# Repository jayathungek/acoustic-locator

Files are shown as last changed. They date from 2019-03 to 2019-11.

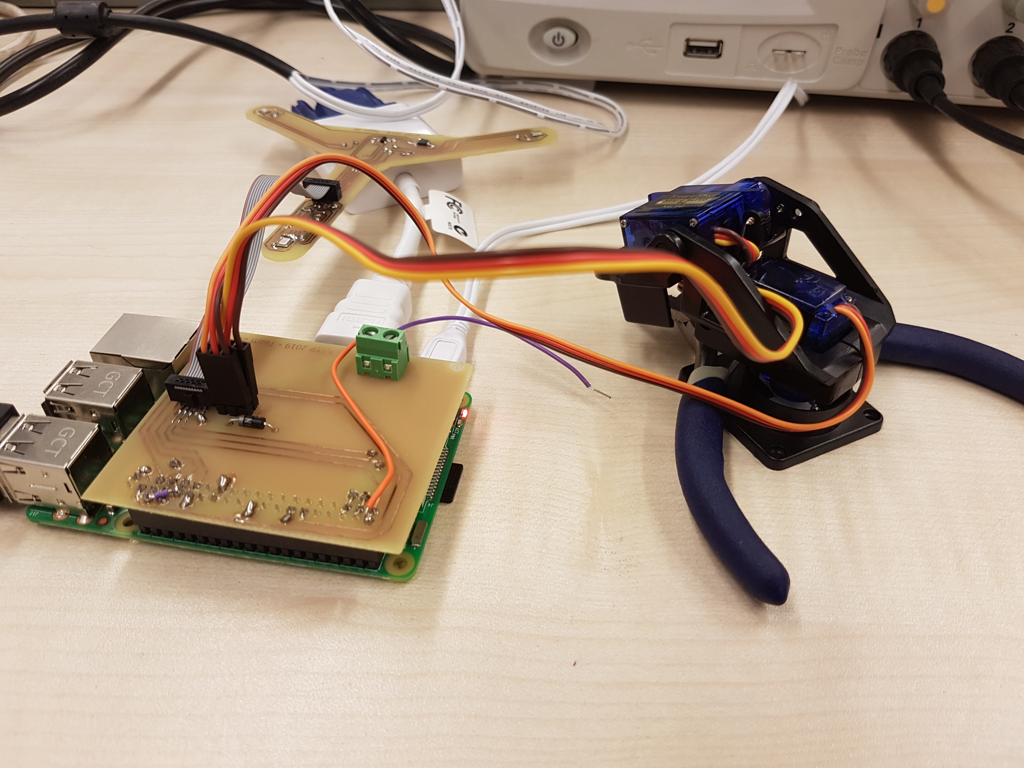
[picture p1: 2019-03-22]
Media/20190313_165925.jpg

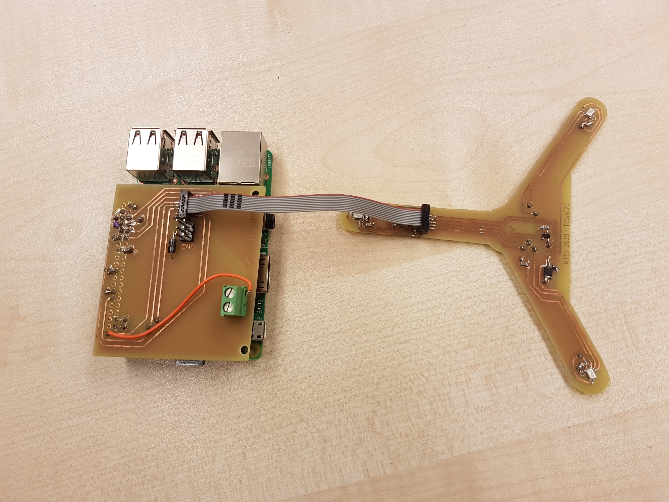
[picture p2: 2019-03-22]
Media/20190313_170128.jpg

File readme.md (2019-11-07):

Table of Contents
=================

   * [acoustic-locator](#acoustic-locator)
      * [Hardware setup](#hardware-setup)
        * [The Microphone Circuit](#the-microphone-circuit)
        * [The Humidity/Temperature Sensor](#the-humiditytemperature-sensor)
        * [The Laser LED circuit](#the-laser-led-circuit)
        * [The Servo Circuit](#the-servo-circuit)
        * [Mechanical Design](#mechanical-design)
      * [Prerequisites](#prerequisites)
      * [Installation](#installation)
      * [How to use](#how-to-use)
      
# acoustic-locator

## Hardware setup

The acoustic locator hardware consists of two basic modules. The first module is the microphone module build on a PCB board that enables the placement of three MEMS microphones. The second module is the positioning module which consists basically of two servo motors, one being responsible for the horizontal movement of the mechanism and the other for the vertical. The front and back views of the acoustic locator are shown in figure 1. The sound source direction detection is achieved with the use of three microphones forming an equilateral triangle. The three holes at the edges of the acoustic locator identified on the front view are the openings for the three microphones. The opening in the middle of the acoustic locator, shown in the front view is the opening for the laser diode. The back view shows the positioning mechanism with the two servo motors.

AL picture

                            Figure 1
                            
 The PCB board for the microphones is shown in figure 2. An IDC connector is used to connect the board with the Raspberry Pi board. The microphones used are Integrated Inter-IC Sound Bus (I2S) compatible digital MEMS microphones. I2S is a serial bus standard/protocol that enable the interface of one or two microphones on a microcontroller through a serial connection. Since the acoustic locator uses three microphones, a multiplexer is used to enable the connection of the microphones on the I2S bus. 

The microphones board also contains the circuit for the humidity/temperature sensor. The reason for using this sensor is because the speed of sound can vary with the temperature and the humidity. If the acoustic locator is used in normal room conditions then there is no need for the temperature/humidity sensor. If the acoustic locator is going to be used in places with extreme temperatures or humidity then the values of the temperature and humidity can be used to calculate the speed of sound and adjust the operation of the acoustic locator accordingly. 

The third module on the microphones PCB board is a laser LED circuit consisting of a LED driver and the laser LED. The laser LED is used for testing purposes, in order to identify the direction at which the acoustic locator is pointing to. On the final product, the laser LED can be replaced by a web camera, so that the camera will point to the person speaking, as explained in the introduction of this report.

Mic_Board

                            Figure 2
                            
### The Microphone Circuit

The microphones used by the acoustic locator are the ICS-43432 digital I2S microphones from InvenSence. The ICS-43432 microphone includes all the required circuitry so that it can be interfaced directly with a microcontroller or a DSP, without the use of an audio codec. As shown in figure 3 the ICS-43432 contains in the same package the MEMS sensor with the signal conditioning circuit, the A/D converter, the anti-aliasing filter and a 24-bit I2S interface. The data sheet, handling information and application notes for the ICS-43432 microphone can be found [here]( https://www.invensense.com/products/digital/ics-43432/).

The ‘Config’ input is used in cases where it is required to modify the internal registers of the device. For normal operation, the ‘Config’ signal must be connected to the ground.  The ‘Left/Right’ (LR) channel select signal is used to specify to which one of the two I2S channels is the microphone connected to. If the L/R pin is connected to the ground (or set to Low), the microphone outputs its signal to the left channel of the I2C frame. If the L/R pin is connected to the supply voltage (or set to High), the microphone outputs its signal to the right channel of the I2C frame.

The I2C signals are the ‘SCK’ (Serial Data Clock for the I2S interface) input signal, the ‘SD’ (Serial Data Output for the I2S interface) signal and the ‘WS’ (Serial Data Word Select for the I2S interface) input signal. If the ‘WS’ signal is set Low, the left microphone sends its data on the ‘SD’ signal, otherwise the right microphone sends its data. The ‘SD’ line must be pull down to the ground using a 100K resistor. A typical circuit with two microphones connected to a DSP or a microcontroller is shown in figure 4.

ICS43432

                              Figure 3
                              
Stereo                              
            
                              Figure 4
                              
The circuit diagram of the acoustic locator microphone board is shown in figure 5. Because the acoustic locator uses three microphones and the I2S interface supports only two, a demultiplexer is used to allow two microphone to share the same I2S channel. The demultiplexer used is the TS3A24159 dual 2-channel SPDT bidirectional analogue switch. As shown in the circuit diagram, the select input (In1) of the analogue switch is connected to the GPIO9 signal of the Raspberry Pi, while the Com input is connected to the WS signal (signal GPIO19).

Setting the In1 pin to low, the WS signal is switched to the WS signal of the Mic1 microphone, thus reading the data from Mic1.  Setting the In1 pin to high, the WS signal is switched to the WS signal of the Mic2 microphone, thus reading the data from Mic2. Since the LR inputs for Mic1 and Mic2 are connected to the supply voltage, both microphones are treated as Right channel microphones. The LS signal of microphone Mic3 is connected to the ground, therefore, this microphone is treated as the Left channel microphone.

Mic_board_Cct(1)

                              Figure 5

### The Humidity/Temperature Sensor

The Humidity/Temperature Sensor used by the acoustic locator is the HIH6030-021-001 digital I2C humidity/temperature from Honeywell. This device combines a humidity and a temperature sensor in the same package. The data sheet, handling information and application notes for the HIH6030-021-001 digital I2C humidity/temperature can be found [here](https://sensing.honeywell.com/HIH6030-021-001-humidity-sensors). 

The pinout with the typical application circuit diagram, given in the device datasheet is shown in figure 13.The same circuit is used  by the acoustic locator as shown in the circuit diagram in figure 5.The SCL pin is connected to the I2C clock, while the SDA pin is connected to the I2C data line. Both the SCL and the SDA pins must be pulled up with a 2.2K resistor each. The supply pin must be decoupled with a 0.1µF capacitor, while the Vcore pin must be connected to the ground through a 0.22µF capacitor. The AL_L (Alarm Low) and the AL_H (Alarm High) pins are used in the case an external device such as a relay or a LED are needed to be controlled directly by the sensor.

Hum_cct

                                Figure 6
                                                           
### The Laser LED circuit

The laser LED circuit, shown in figure 7, consists of the laser diode, MOSFET transistor driver and resistor. The transistor driver is used because the Raspberry Pi cannot provide the amount of current required to operate the laser LED. The resistor is used to limit the current through the laser to the value lower than the maximum LED current. The operation of the laser is achieved by controlling the state of the GPIO6 of the Raspberry Pi.

laser

                                Figure 7
                                
### The Servo Circuit

The movement of the positioning mechanism is achieved by the use of two servo motors. These motors are connected by the Raspberry Pi, through a board that is attached on the Raspberry Pi as a shield shown in figure 8. This shield also provides a connection from the Raspberry Pi to the microphones board through an IDC connector and a ribbon cable.The circuit diagram for the connection of the two servo motors to the Raspberry Pi is shown in figure 9. The speed and direction of rotation of the servo motors is achieved through the PWM signals obtained from the GPIO12 and the GPIO13 signals of the Raspberry Pi.

RPShield

                                Figure 8
                                
servocct

                                Figure 9
                                
### Mechanical Design

The mechanical design consists of the direction mechanism. This design features three parts: (a) the base, (b) a gimbal and (c) the head.

The base serves two functions: it supports the device as well as houses the Raspberry Pi, along with the locator interface board. The design allows the Raspberry Pi to be connected to a PC/laptop without opening the base.
The pan/tilt gimbal aids the movement of the device. It is capable of 180° rotation around the vertical axis as well as 100° up and down. The gimbal is mounts on top of the base as well as holding the head.

The head – a 3D printed part – clicks in place on top of the gimbal. The part is designed to secure the microphones in their respective places. The PCB just slides intro the head, thus no screws are required to hold the electronics on the gimbal.

## Prerequisites
The following steps are needed to configure the raspberry pi for I2S microphone support:

1. Enable I2S communication:- 
  ```
  $ sudo nano /boot/config.txt
  ```
  1.1 Navigate the file and uncomment the the line that contains `#dtparam=i2s=on`. 
  
2. Add the reference for the chip on the Raspberry Pi 3 that handles the I2S into the modules file:- 
  ```
  $ sudo nano  /etc/modules
  ``` 
  2.1 Add the line `snd-bcm2835` to this file.
  
3. Reboot:- 
  ```
  $ sudo reboot
  ```
  
4. Run this command and verify that it outputs `snd_soc_bcm2835_i2s`:-
  ```
  $ lsmod | grep snd
  ```
  
5. Install dependancies and set permissions:- 
  ```
  $ sudo apt-get -y install bc libncurses5-dev
  $ sudo wget https://raw.githubusercontent.com/notro/rpi-source/master/rpi-source -O /usr/bin/rpi-source`
  $ sudo chmod +x /usr/bin/rpi-source
  ```
6. Update `rpi-source` and run:-
  ```
  $ /usr/bin/rpi-source -q --tag-update`
  $ rpi-source
  ```
  
7. Mount the developent system debugger:-
  ```$ sudo mount -t debugfs debugs /sys/kernel/debug```
  
8. Check for the presence of the 3f203000.i2s module:-
  ```$ sudo cat /sys/kernel/debug/asoc/platforms```
  
9. Download Paul Creaser's I2S audio module, navigate to it and build it:-
  ```
  $ git clone https://github.com/PaulCreaser/rpi-i2s-audio
  $ cd rpi-i2s-audio
  $ make -C /lib/modules/$(uname -r )/build M=$(pwd) modules
  ```
  
10. Insert this module and verify its presence:-
  ```
  $ sudo insmod my_loader.ko
  $ lsmod | grep my_loader
  $ dmesg | tail
  ```
  
11. To load the module every time the pi is booted up:-
  ```
  $ sudo cp my_loader.ko /lib/modules/$(uname -r)
  $ echo 'my_loader' | sudo tee --append /etc/modules > /dev/null
  $ sudo depmod -a
  $ sudo modprobe my_loader
  ```

## Installation
1. Clone this repository: `$ git clone git@github.com:jayathungek/acoustic-locator.git`
2. Navigate to the main directory: `$ cd acoustic-locator`
3. Run tests: `$ make runtests`. All the tests should pass.
4. Build: `$ make`

A binary called `locator` is generated in the current working directory. Running this with `$ sudo ./locator` will start the main loop of the program and the gimbals will move in response to loud noises. Alternatively, f you wish to run `locator` on boot, edit `/etc/rc.local` so that it contains the path to the binary:
   ```
   #!/bin/sh -e
   #
   # rc.local
   #
   # This script is executed at the end of each multiuser runlevel.
   # Make sure that the script will "exit 0" on success or any other
   # value on error. 
   #
   # In order to enable or disable this script just change the execution
   # bits.
   #
   # By default this script does nothing.

   sudo /home/pi/acoustic-locator/locator &

   exit 0
   ```

## How to use
The raspberry pi is powered by a 5V micro usb cable and is perfectly capable of driving the servo motors from its 5V pins. Assuming all the steps above have been followed, simply plugging in the device to any 5V DC supply will start the location program.

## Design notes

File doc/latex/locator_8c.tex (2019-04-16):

\hypertarget{locator_8c}{}\doxysection{locator.\+c File Reference}
\label{locator_8c}\index{locator.c@{locator.c}}
{\ttfamily \#include $<$stdio.\+h$>$}\newline
{\ttfamily \#include $<$signal.\+h$>$}\newline
{\ttfamily \#include $<$stdlib.\+h$>$}\newline
{\ttfamily \#include $<$unistd.\+h$>$}\newline
{\ttfamily \#include $<$math.\+h$>$}\newline
{\ttfamily \#include $<$wiring\+Pi.\+h$>$}\newline
{\ttfamily \#include $<$alsa/asoundlib.\+h$>$}\newline
{\ttfamily \#include \char`\"{}servo.\+h\char`\"{}}\newline
{\ttfamily \#include \char`\"{}utils.\+h\char`\"{}}\newline
\doxysubsection*{Macros}
\begin{DoxyCompactItemize}
\item 
\#define \mbox{\hyperlink{locator_8c_a775d096fbc3988fb7ed858b79ef44e22}{D\+E\+V\+I\+CE}}~\char`\"{}plughw\+:1\char`\"{}
\begin{DoxyCompactList}\small\item\em Name of the A\+L\+SA P\+CM device. \end{DoxyCompactList}\item 
\#define \mbox{\hyperlink{locator_8c_a51a51480d875f80355412fa95fd48c6c}{F\+R\+A\+M\+ES}}~256
\begin{DoxyCompactList}\small\item\em Number of frames to read in. \end{DoxyCompactList}\item 
\#define \mbox{\hyperlink{locator_8c_a4679d8ea8690999a6c6c7c0cb245c879}{T\+H\+R\+E\+S\+H\+O\+LD}}~30000
\begin{DoxyCompactList}\small\item\em Minimum detectable sound pressure level. \end{DoxyCompactList}\item 
\#define \mbox{\hyperlink{locator_8c_a538e0cad3acb787a49e16b1e53787610}{S\+A\+M\+P\+L\+E\+R\+A\+TE}}~44100
\begin{DoxyCompactList}\small\item\em Audio sampling frequency (Hz) \end{DoxyCompactList}\item 
\#define \mbox{\hyperlink{locator_8c_a9b0d77bf55bf55aeb2c144a2d7e63339}{T\+O\+P1}}~0
\begin{DoxyCompactList}\small\item\em Enumeration for top microphone buffer. \end{DoxyCompactList}\item 
\#define \mbox{\hyperlink{locator_8c_af7b10168e3d3a294b97e26c36e662d55}{T\+O\+P2}}~1
\begin{DoxyCompactList}\small\item\em Enumeration for top microphone buffer. \end{DoxyCompactList}\item 
\#define \mbox{\hyperlink{locator_8c_a437ef08681e7210d6678427030446a54}{L\+E\+FT}}~2
\begin{DoxyCompactList}\small\item\em Enumeration for left microphone buffer. \end{DoxyCompactList}\item 
\#define \mbox{\hyperlink{locator_8c_a80fb826a684cf3f0d306b22aa100ddac}{R\+I\+G\+HT}}~3
\begin{DoxyCompactList}\small\item\em Enumeration for right microphone buffer. \end{DoxyCompactList}\item 
\#define \mbox{\hyperlink{locator_8c_a725b2d406a9e08983d25ebc6f6bfb02d}{M\+U\+X\+SE}}~21
\begin{DoxyCompactList}\small\item\em wiring\+Pi pin connected to multiplexer. \end{DoxyCompactList}\end{DoxyCompactItemize}
\doxysubsection*{Functions}
\begin{DoxyCompactItemize}
\item 
void \mbox{\hyperlink{locator_8c_a5e250a67c49473a3c4b02995be1d5655}{printbuf}} (signed int $\ast$buf, int size)
\begin{DoxyCompactList}\small\item\em A function that takes an integer buffer and renders its contents to sdout for debugging. \end{DoxyCompactList}\item 
void \mbox{\hyperlink{locator_8c_afab5f34a4aca7b851d41424729988c53}{print\+Buf\+To\+File}} (F\+I\+LE $\ast$file, signed int $\ast$buf, int size)
\begin{DoxyCompactList}\small\item\em A function that takes an integer buffer and renders its contents to the specified file descriptor for debugging. \end{DoxyCompactList}\item 
void \mbox{\hyperlink{locator_8c_a6633207217364c8d34a60d09de941625}{fillbuf}} (int tobuf\+Code, int $\ast$tobuf, char $\ast$frombuf, int sizefrom)
\begin{DoxyCompactList}\small\item\em Splits data in the P\+CM buffer so that the correct channel is sent to the destination buffer. \end{DoxyCompactList}\item 
int \mbox{\hyperlink{locator_8c_a2b5886eb22ba27b612c693d9f6ed9228}{setupdevice}} (char $\ast$device, unsigned int rate)
\begin{DoxyCompactList}\small\item\em Initialises the A\+L\+SA P\+CM interface. \end{DoxyCompactList}\item 
int \mbox{\hyperlink{locator_8c_a153f2dd1fc7aefa8daa15ea644641b43}{setupmicbuffers}} (int \mbox{\hyperlink{locator_8c_a281c5134f826917fef45ddaf523ce49a}{frames}}, int $\ast$pcm\+\_\+size, int $\ast$mic\+\_\+size)
\begin{DoxyCompactList}\small\item\em Allocates memory for P\+CM and mic data buffers. \end{DoxyCompactList}\item 
void \mbox{\hyperlink{locator_8c_a49138c5791a45f3d722eb19390839c34}{freebuffers}} ()
\begin{DoxyCompactList}\small\item\em Frees memory allocated to P\+CM and mic data buffers. \end{DoxyCompactList}\item 
void \mbox{\hyperlink{locator_8c_a53d63e1aafd4fe1439cfc392bd97fb07}{read\+Mics}} ()
\begin{DoxyCompactList}\small\item\em Updates top1, left, top2 and right buffers. \end{DoxyCompactList}\item 
void \mbox{\hyperlink{locator_8c_af5a49d591667a22acf6b75ee6236c3be}{update\+Position}} (float del\+TL, float del\+TR, float del\+LR)
\begin{DoxyCompactList}\small\item\em Moves servos in response to timing difference data. \end{DoxyCompactList}\item 
int \mbox{\hyperlink{locator_8c_a0ddf1224851353fc92bfbff6f499fa97}{main}} (int argc, char $\ast$argv\mbox{[}$\,$\mbox{]})
\item 
void \mbox{\hyperlink{locator_8c_a73fb9687dd54fc486114ef158fa29330}{read\+Mics}} (int $\ast$\mbox{\hyperlink{locator_8c_a195834fe831b25227f2ed54948dc06e9}{top1}}, int $\ast$\mbox{\hyperlink{locator_8c_a3d953171fbedb4b128bd6fe5e6257f49}{left}}, int $\ast$\mbox{\hyperlink{locator_8c_aa489c260f2bf8edb93576e1d945fed13}{top2}}, int $\ast$\mbox{\hyperlink{locator_8c_aa246ca2e7708de6457661f06ff4ecf8f}{right}})
\end{DoxyCompactItemize}
\doxysubsection*{Variables}
\begin{DoxyCompactItemize}
\item 
F\+I\+LE $\ast$ \mbox{\hyperlink{locator_8c_a1277960b5f2b37137fe9b0b5a1ea0beb}{out}}
\item 
int \mbox{\hyperlink{locator_8c_ac3e1795766a80ec63b157951b4b9a7d4}{debug}} = 0
\item 
snd\+\_\+pcm\+\_\+t $\ast$ \mbox{\hyperlink{locator_8c_a8530736c0c7f7f4dc724c8246e301f83}{handle}}
\item 
snd\+\_\+pcm\+\_\+hw\+\_\+params\+\_\+t $\ast$ \mbox{\hyperlink{locator_8c_a651b4eec34e0ce0ad2b7234fe1689fcb}{params}}
\item 
snd\+\_\+pcm\+\_\+uframes\+\_\+t \mbox{\hyperlink{locator_8c_a281c5134f826917fef45ddaf523ce49a}{frames}} = \mbox{\hyperlink{locator_8c_a51a51480d875f80355412fa95fd48c6c}{F\+R\+A\+M\+ES}}
\item 
unsigned int \mbox{\hyperlink{locator_8c_a1c086f81c095b0efd7a87ee29fc5ba7e}{sample\+\_\+rate}}
\item 
int \mbox{\hyperlink{locator_8c_a7afcac3447636c03934613716685bbc8}{sel}}
\item 
char $\ast$ \mbox{\hyperlink{locator_8c_aff2566f4c366b48d73479bef43ee4d2e}{buffer}}
\item 
signed int $\ast$ \mbox{\hyperlink{locator_8c_a195834fe831b25227f2ed54948dc06e9}{top1}}
\begin{DoxyCompactList}\small\item\em Buffer for top mic. \end{DoxyCompactList}\item 
signed int $\ast$ \mbox{\hyperlink{locator_8c_aa489c260f2bf8edb93576e1d945fed13}{top2}}
\begin{DoxyCompactList}\small\item\em Buffer for top mic. \end{DoxyCompactList}\item 
signed int $\ast$ \mbox{\hyperlink{locator_8c_a3d953171fbedb4b128bd6fe5e6257f49}{left}}
\begin{DoxyCompactList}\small\item\em Buffer for left mic. \end{DoxyCompactList}\item 
signed int $\ast$ \mbox{\hyperlink{locator_8c_aa246ca2e7708de6457661f06ff4ecf8f}{right}}
\begin{DoxyCompactList}\small\item\em Buffer for right mic. \end{DoxyCompactList}\item 
int \mbox{\hyperlink{locator_8c_a1f14db325606d8f825754cff1cc21123}{pcm\+\_\+bufsize}} = 0
\item 
int \mbox{\hyperlink{locator_8c_ab6adac1d000df58e1f54bfef3f2d5081}{mic\+\_\+bufsize}} = 0
\item 
int \mbox{\hyperlink{locator_8c_af15ce0e091b409de25694109f11f484b}{az\+\_\+curr}} = 0
\item 
int \mbox{\hyperlink{locator_8c_adfd48dc66211fce52f7d14f4e780ae02}{el\+\_\+curr}} = 0
\item 
int \mbox{\hyperlink{locator_8c_a4daf39371ce88e725afdddef077ad0da}{zero\+Top1}}
\begin{DoxyCompactList}\small\item\em Index of zero crossing in top1 mic buffer. \end{DoxyCompactList}\item 
int \mbox{\hyperlink{locator_8c_a81e715298ef2793d7133ced346aae6e5}{zero\+Left}}
\begin{DoxyCompactList}\small\item\em Index of zero crossing in left mic buffer. \end{DoxyCompactList}\item 
int \mbox{\hyperlink{locator_8c_ab7af76e9f538eb8576c1435dccd847d1}{zero\+Top2}}
\begin{DoxyCompactList}\small\item\em Index of zero crossing in top2 mic buffer. \end{DoxyCompactList}\item 
int \mbox{\hyperlink{locator_8c_a6803a267f65c0269820bd931dae3f2f2}{zero\+Right}}
\begin{DoxyCompactList}\small\item\em Index of zero crossing in right mic buffer. \end{DoxyCompactList}\item 
float \mbox{\hyperlink{locator_8c_a196c0e2744accf42066216c9452ab1af}{del\+Top\+Left}}
\begin{DoxyCompactList}\small\item\em Time delay of zero crossing between top and left mics (seconds). \end{DoxyCompactList}\item 
float \mbox{\hyperlink{locator_8c_afcc32c167cbf0821f350aee6ac4fb972}{del\+Top\+Right}}
\begin{DoxyCompactList}\small\item\em Time delay of zero crossing between top and right mics (seconds). \end{DoxyCompactList}\item 
float \mbox{\hyperlink{locator_8c_a4ae30cc36621a0f0c56004247084b155}{del\+Left\+Right}}
\begin{DoxyCompactList}\small\item\em Time delay of zero crossing between left and right mics (seconds). \end{DoxyCompactList}\end{DoxyCompactItemize}

\doxysubsection{Macro Definition Documentation}
\mbox{\Hypertarget{locator_8c_a775d096fbc3988fb7ed858b79ef44e22}\label{locator_8c_a775d096fbc3988fb7ed858b79ef44e22}} 
\index{locator.c@{locator.c}!DEVICE@{DEVICE}}
\index{DEVICE@{DEVICE}!locator.c@{locator.c}}
\doxysubsubsection{\texorpdfstring{DEVICE}{DEVICE}}
{\footnotesize\ttfamily \#define D\+E\+V\+I\+CE~\char`\"{}plughw\+:1\char`\"{}}

Name of the A\+L\+SA P\+CM device. 

\mbox{\Hypertarget{locator_8c_a51a51480d875f80355412fa95fd48c6c}\label{locator_8c_a51a51480d875f80355412fa95fd48c6c}} 
\index{locator.c@{locator.c}!FRAMES@{FRAMES}}
\index{FRAMES@{FRAMES}!locator.c@{locator.c}}
\doxysubsubsection{\texorpdfstring{FRAMES}{FRAMES}}
{\footnotesize\ttfamily \#define F\+R\+A\+M\+ES~256}

Number of frames to read in. 

Frames contain both left-\/ and right-\/channel samples and are read into the P\+CM buffer \mbox{\Hypertarget{locator_8c_a437ef08681e7210d6678427030446a54}\label{locator_8c_a437ef08681e7210d6678427030446a54}} 
\index{locator.c@{locator.c}!LEFT@{LEFT}}
\index{LEFT@{LEFT}!locator.c@{locator.c}}
\doxysubsubsection{\texorpdfstring{LEFT}{LEFT}}
{\footnotesize\ttfamily \#define L\+E\+FT~2}

Enumeration for left microphone buffer. 

\mbox{\Hypertarget{locator_8c_a725b2d406a9e08983d25ebc6f6bfb02d}\label{locator_8c_a725b2d406a9e08983d25ebc6f6bfb02d}} 
\index{locator.c@{locator.c}!MUXSE@{MUXSE}}
\index{MUXSE@{MUXSE}!locator.c@{locator.c}}
\doxysubsubsection{\texorpdfstring{MUXSE}{MUXSE}}
{\footnotesize\ttfamily \#define M\+U\+X\+SE~21}

wiring\+Pi pin connected to multiplexer. 

\mbox{\Hypertarget{locator_8c_a80fb826a684cf3f0d306b22aa100ddac}\label{locator_8c_a80fb826a684cf3f0d306b22aa100ddac}} 
\index{locator.c@{locator.c}!RIGHT@{RIGHT}}
\index{RIGHT@{RIGHT}!locator.c@{locator.c}}
\doxysubsubsection{\texorpdfstring{RIGHT}{RIGHT}}
{\footnotesize\ttfamily \#define R\+I\+G\+HT~3}

Enumeration for right microphone buffer. 

\mbox{\Hypertarget{locator_8c_a538e0cad3acb787a49e16b1e53787610}\label{locator_8c_a538e0cad3acb787a49e16b1e53787610}} 
\index{locator.c@{locator.c}!SAMPLERATE@{SAMPLERATE}}
\index{SAMPLERATE@{SAMPLERATE}!locator.c@{locator.c}}
\doxysubsubsection{\texorpdfstring{SAMPLERATE}{SAMPLERATE}}
{\footnotesize\ttfamily \#define S\+A\+M\+P\+L\+E\+R\+A\+TE~44100}

Audio sampling frequency (Hz) 

\mbox{\Hypertarget{locator_8c_a4679d8ea8690999a6c6c7c0cb245c879}\label{locator_8c_a4679d8ea8690999a6c6c7c0cb245c879}} 
\index{locator.c@{locator.c}!THRESHOLD@{THRESHOLD}}
\index{THRESHOLD@{THRESHOLD}!locator.c@{locator.c}}
\doxysubsubsection{\texorpdfstring{THRESHOLD}{THRESHOLD}}
{\footnotesize\ttfamily \#define T\+H\+R\+E\+S\+H\+O\+LD~30000}

Minimum detectable sound pressure level. 

\mbox{\Hypertarget{locator_8c_a9b0d77bf55bf55aeb2c144a2d7e63339}\label{locator_8c_a9b0d77bf55bf55aeb2c144a2d7e63339}} 
\index{locator.c@{locator.c}!TOP1@{TOP1}}
\index{TOP1@{TOP1}!locator.c@{locator.c}}
\doxysubsubsection{\texorpdfstring{TOP1}{TOP1}}
{\footnotesize\ttfamily \#define T\+O\+P1~0}

Enumeration for top microphone buffer. 

(Multiplexer select = 0) \mbox{\Hypertarget{locator_8c_af7b10168e3d3a294b97e26c36e662d55}\label{locator_8c_af7b10168e3d3a294b97e26c36e662d55}} 
\index{locator.c@{locator.c}!TOP2@{TOP2}}
\index{TOP2@{TOP2}!locator.c@{locator.c}}
\doxysubsubsection{\texorpdfstring{TOP2}{TOP2}}
{\footnotesize\ttfamily \#define T\+O\+P2~1}

Enumeration for top microphone buffer. 

(Multiplexer select = 1) 

\doxysubsection{Function Documentation}
\mbox{\Hypertarget{locator_8c_a6633207217364c8d34a60d09de941625}\label{locator_8c_a6633207217364c8d34a60d09de941625}} 
\index{locator.c@{locator.c}!fillbuf@{fillbuf}}
\index{fillbuf@{fillbuf}!locator.c@{locator.c}}
\doxysubsubsection{\texorpdfstring{fillbuf()}{fillbuf()}}
{\footnotesize\ttfamily void fillbuf (\begin{DoxyParamCaption}\item[{int}]{tobuf\+Code,  }\item[{int $\ast$}]{tobuf,  }\item[{char $\ast$}]{frombuf,  }\item[{int}]{sizefrom }\end{DoxyParamCaption})}

Splits data in the P\+CM buffer so that the correct channel is sent to the destination buffer. 

\begin{DoxyParams}{Parameters}
{\em tobuf\+Code} & Character code for destination buffer \\
\hline
{\em tobuf} & Pointer to destination buffer \\
\hline
{\em frombuf} & Pointer to P\+CM buffer \\
\hline
{\em sizefrom} & Size of P\+CM buffer \\
\hline
\end{DoxyParams}
\begin{DoxySeeAlso}{See also}
\mbox{\hyperlink{locator_8c_a195834fe831b25227f2ed54948dc06e9}{top1}} 

\mbox{\hyperlink{locator_8c_aa489c260f2bf8edb93576e1d945fed13}{top2}} 

\mbox{\hyperlink{locator_8c_a3d953171fbedb4b128bd6fe5e6257f49}{left}} 

\mbox{\hyperlink{locator_8c_aa246ca2e7708de6457661f06ff4ecf8f}{right}} 
\end{DoxySeeAlso}
\mbox{\Hypertarget{locator_8c_a49138c5791a45f3d722eb19390839c34}\label{locator_8c_a49138c5791a45f3d722eb19390839c34}} 
\index{locator.c@{locator.c}!freebuffers@{freebuffers}}
\index{freebuffers@{freebuffers}!locator.c@{locator.c}}
\doxysubsubsection{\texorpdfstring{freebuffers()}{freebuffers()}}
{\footnotesize\ttfamily void freebuffers (\begin{DoxyParamCaption}{ }\end{DoxyParamCaption})}

Frees memory allocated to P\+CM and mic data buffers. 

\mbox{\Hypertarget{locator_8c_a0ddf1224851353fc92bfbff6f499fa97}\label{locator_8c_a0ddf1224851353fc92bfbff6f499fa97}} 
\index{locator.c@{locator.c}!main@{main}}
\index{main@{main}!locator.c@{locator.c}}
\doxysubsubsection{\texorpdfstring{main()}{main()}}
{\footnotesize\ttfamily int main (\begin{DoxyParamCaption}\item[{int}]{argc,  }\item[{char $\ast$}]{argv\mbox{[}$\,$\mbox{]} }\end{DoxyParamCaption})}

\mbox{\Hypertarget{locator_8c_a5e250a67c49473a3c4b02995be1d5655}\label{locator_8c_a5e250a67c49473a3c4b02995be1d5655}} 
\index{locator.c@{locator.c}!printbuf@{printbuf}}
\index{printbuf@{printbuf}!locator.c@{locator.c}}
\doxysubsubsection{\texorpdfstring{printbuf()}{printbuf()}}
{\footnotesize\ttfamily void printbuf (\begin{DoxyParamCaption}\item[{signed int $\ast$}]{buf,  }\item[{int}]{size }\end{DoxyParamCaption})}

A function that takes an integer buffer and renders its contents to sdout for debugging. 

\begin{DoxyParams}{Parameters}
{\em buf} & A pointer to the buffer. \\
\hline
{\em size} & The number of elements in the array. \\
\hline
\end{DoxyParams}
\mbox{\Hypertarget{locator_8c_afab5f34a4aca7b851d41424729988c53}\label{locator_8c_afab5f34a4aca7b851d41424729988c53}} 
\index{locator.c@{locator.c}!printBufToFile@{printBufToFile}}
\index{printBufToFile@{printBufToFile}!locator.c@{locator.c}}
\doxysubsubsection{\texorpdfstring{printBufToFile()}{printBufToFile()}}
{\footnotesize\ttfamily void print\+Buf\+To\+File (\begin{DoxyParamCaption}\item[{F\+I\+LE $\ast$}]{file,  }\item[{signed int $\ast$}]{buf,  }\item[{int}]{size }\end{DoxyParamCaption})}

A function that takes an integer buffer and renders its contents to the specified file descriptor for debugging. 

\begin{DoxyParams}{Parameters}
{\em file} & A pointer to a file descriptor. \\
\hline
{\em buf} & A pointer to a signed integer. \\
\hline
{\em size} & The number of elements in the array. \\
\hline
\end{DoxyParams}
\mbox{\Hypertarget{locator_8c_a53d63e1aafd4fe1439cfc392bd97fb07}\label{locator_8c_a53d63e1aafd4fe1439cfc392bd97fb07}} 
\index{locator.c@{locator.c}!readMics@{readMics}}
\index{readMics@{readMics}!locator.c@{locator.c}}
\doxysubsubsection{\texorpdfstring{readMics()}{readMics()}\hspace{0.1cm}{\footnotesize\ttfamily [1/2]}}
{\footnotesize\ttfamily void read\+Mics (\begin{DoxyParamCaption}{ }\end{DoxyParamCaption})}

Updates top1, left, top2 and right buffers. 

\mbox{\Hypertarget{locator_8c_a73fb9687dd54fc486114ef158fa29330}\label{locator_8c_a73fb9687dd54fc486114ef158fa29330}} 
\index{locator.c@{locator.c}!readMics@{readMics}}
\index{readMics@{readMics}!locator.c@{locator.c}}
\doxysubsubsection{\texorpdfstring{readMics()}{readMics()}\hspace{0.1cm}{\footnotesize\ttfamily [2/2]}}
{\footnotesize\ttfamily void read\+Mics (\begin{DoxyParamCaption}\item[{int $\ast$}]{top1,  }\item[{int $\ast$}]{left,  }\item[{int $\ast$}]{top2,  }\item[{int $\ast$}]{right }\end{DoxyParamCaption})}

\mbox{\Hypertarget{locator_8c_a2b5886eb22ba27b612c693d9f6ed9228}\label{locator_8c_a2b5886eb22ba27b612c693d9f6ed9228}} 
\index{locator.c@{locator.c}!setupdevice@{setupdevice}}
\index{setupdevice@{setupdevice}!locator.c@{locator.c}}
\doxysubsubsection{\texorpdfstring{setupdevice()}{setupdevice()}}
{\footnotesize\ttfamily int setupdevice (\begin{DoxyParamCaption}\item[{char $\ast$}]{device,  }\item[{unsigned int}]{rate }\end{DoxyParamCaption})}

Initialises the A\+L\+SA P\+CM interface. 

\begin{DoxyParams}{Parameters}
{\em device} & Name of the I2S device \\
\hline
{\em rate} & Audio sampling rate (Hz) \\
\hline
\end{DoxyParams}
\begin{DoxyReturn}{Returns}
Error code (0 on success) 
\end{DoxyReturn}
\mbox{\Hypertarget{locator_8c_a153f2dd1fc7aefa8daa15ea644641b43}\label{locator_8c_a153f2dd1fc7aefa8daa15ea644641b43}} 
\index{locator.c@{locator.c}!setupmicbuffers@{setupmicbuffers}}
\index{setupmicbuffers@{setupmicbuffers}!locator.c@{locator.c}}
\doxysubsubsection{\texorpdfstring{setupmicbuffers()}{setupmicbuffers()}}
{\footnotesize\ttfamily int setupmicbuffers (\begin{DoxyParamCaption}\item[{int}]{frames,  }\item[{int $\ast$}]{pcm\+\_\+size,  }\item[{int $\ast$}]{mic\+\_\+size }\end{DoxyParamCaption})}

Allocates memory for P\+CM and mic data buffers. 

@ param frames The number of frames in the P\+CM buffer @ param pcm\+\_\+size A pointer to the integer that contains the pcm buffer size @ param mic\+\_\+size A pointer to the integer that contains the pcm buffer size @ return Error code (0 on success) \mbox{\Hypertarget{locator_8c_af5a49d591667a22acf6b75ee6236c3be}\label{locator_8c_af5a49d591667a22acf6b75ee6236c3be}} 
\index{locator.c@{locator.c}!updatePosition@{updatePosition}}
\index{updatePosition@{updatePosition}!locator.c@{locator.c}}
\doxysubsubsection{\texorpdfstring{updatePosition()}{updatePosition()}}
{\footnotesize\ttfamily void update\+Position (\begin{DoxyParamCaption}\item[{float}]{del\+TL,  }\item[{float}]{del\+TR,  }\item[{float}]{del\+LR }\end{DoxyParamCaption})}

Moves servos in response to timing difference data. 

\begin{DoxyParams}{Parameters}
{\em del\+TL} & Time difference between sound reaching top and left mics (seconds) \\
\hline
{\em del\+TR} & Time difference between sound reaching top and right mics (seconds) \\
\hline
{\em del\+LR} & Time difference between sound reaching left and right mics (seconds) \\
\hline
\end{DoxyParams}

\doxysubsection{Variable Documentation}
\mbox{\Hypertarget{locator_8c_af15ce0e091b409de25694109f11f484b}\label{locator_8c_af15ce0e091b409de25694109f11f484b}} 
\index{locator.c@{locator.c}!az\_curr@{az\_curr}}
\index{az\_curr@{az\_curr}!locator.c@{locator.c}}
\doxysubsubsection{\texorpdfstring{az\_curr}{az\_curr}}
{\footnotesize\ttfamily int az\+\_\+curr = 0}

\mbox{\Hypertarget{locator_8c_aff2566f4c366b48d73479bef43ee4d2e}\label{locator_8c_aff2566f4c366b48d73479bef43ee4d2e}} 
\index{locator.c@{locator.c}!buffer@{buffer}}
\index{buffer@{buffer}!locator.c@{locator.c}}
\doxysubsubsection{\texorpdfstring{buffer}{buffer}}
{\footnotesize\ttfamily char$\ast$ buffer}

\mbox{\Hypertarget{locator_8c_ac3e1795766a80ec63b157951b4b9a7d4}\label{locator_8c_ac3e1795766a80ec63b157951b4b9a7d4}} 
\index{locator.c@{locator.c}!debug@{debug}}
\index{debug@{debug}!locator.c@{locator.c}}
\doxysubsubsection{\texorpdfstring{debug}{debug}}
{\footnotesize\ttfamily int debug = 0}

\mbox{\Hypertarget{locator_8c_a4ae30cc36621a0f0c56004247084b155}\label{locator_8c_a4ae30cc36621a0f0c56004247084b155}} 
\index{locator.c@{locator.c}!delLeftRight@{delLeftRight}}
\index{delLeftRight@{delLeftRight}!locator.c@{locator.c}}
\doxysubsubsection{\texorpdfstring{delLeftRight}{delLeftRight}}
{\footnotesize\ttfamily float del\+Left\+Right}

Time delay of zero crossing between left and right mics (seconds). 

\mbox{\Hypertarget{locator_8c_a196c0e2744accf42066216c9452ab1af}\label{locator_8c_a196c0e2744accf42066216c9452ab1af}} 
\index{locator.c@{locator.c}!delTopLeft@{delTopLeft}}
\index{delTopLeft@{delTopLeft}!locator.c@{locator.c}}
\doxysubsubsection{\texorpdfstring{delTopLeft}{delTopLeft}}
{\footnotesize\ttfamily float del\+Top\+Left}

Time delay of zero crossing between top and left mics (seconds). 

\mbox{\Hypertarget{locator_8c_afcc32c167cbf0821f350aee6ac4fb972}\label{locator_8c_afcc32c167cbf0821f350aee6ac4fb972}} 
\index{locator.c@{locator.c}!delTopRight@{delTopRight}}
\index{delTopRight@{delTopRight}!locator.c@{locator.c}}
\doxysubsubsection{\texorpdfstring{delTopRight}{delTopRight}}
{\footnotesize\ttfamily float del\+Top\+Right}

Time delay of zero crossing between top and right mics (seconds). 

\mbox{\Hypertarget{locator_8c_adfd48dc66211fce52f7d14f4e780ae02}\label{locator_8c_adfd48dc66211fce52f7d14f4e780ae02}} 
\index{locator.c@{locator.c}!el\_curr@{el\_curr}}
\index{el\_curr@{el\_curr}!locator.c@{locator.c}}
\doxysubsubsection{\texorpdfstring{el\_curr}{el\_curr}}
{\footnotesize\ttfamily int el\+\_\+curr = 0}

\mbox{\Hypertarget{locator_8c_a281c5134f826917fef45ddaf523ce49a}\label{locator_8c_a281c5134f826917fef45ddaf523ce49a}} 
\index{locator.c@{locator.c}!frames@{frames}}
\index{frames@{frames}!locator.c@{locator.c}}
\doxysubsubsection{\texorpdfstring{frames}{frames}}
{\footnotesize\ttfamily snd\+\_\+pcm\+\_\+uframes\+\_\+t frames = \mbox{\hyperlink{locator_8c_a51a51480d875f80355412fa95fd48c6c}{F\+R\+A\+M\+ES}}}

\mbox{\Hypertarget{locator_8c_a8530736c0c7f7f4dc724c8246e301f83}\label{locator_8c_a8530736c0c7f7f4dc724c8246e301f83}} 
\index{locator.c@{locator.c}!handle@{handle}}
\index{handle@{handle}!locator.c@{locator.c}}
\doxysubsubsection{\texorpdfstring{handle}{handle}}
{\footnotesize\ttfamily snd\+\_\+pcm\+\_\+t$\ast$ handle}

\mbox{\Hypertarget{locator_8c_a3d953171fbedb4b128bd6fe5e6257f49}\label{locator_8c_a3d953171fbedb4b128bd6fe5e6257f49}} 
\index{locator.c@{locator.c}!left@{left}}
\index{left@{left}!locator.c@{locator.c}}
\doxysubsubsection{\texorpdfstring{left}{left}}
{\footnotesize\ttfamily signed int$\ast$ left}

Buffer for left mic. 

This buffer is read into when the multiplexer select is 0. \mbox{\Hypertarget{locator_8c_ab6adac1d000df58e1f54bfef3f2d5081}\label{locator_8c_ab6adac1d000df58e1f54bfef3f2d5081}} 
\index{locator.c@{locator.c}!mic\_bufsize@{mic\_bufsize}}
\index{mic\_bufsize@{mic\_bufsize}!locator.c@{locator.c}}
\doxysubsubsection{\texorpdfstring{mic\_bufsize}{mic\_bufsize}}
{\footnotesize\ttfamily int mic\+\_\+bufsize = 0}

\mbox{\Hypertarget{locator_8c_a1277960b5f2b37137fe9b0b5a1ea0beb}\label{locator_8c_a1277960b5f2b37137fe9b0b5a1ea0beb}} 
\index{locator.c@{locator.c}!out@{out}}
\index{out@{out}!locator.c@{locator.c}}
\doxysubsubsection{\texorpdfstring{out}{out}}
{\footnotesize\ttfamily F\+I\+LE$\ast$ out}

\mbox{\Hypertarget{locator_8c_a651b4eec34e0ce0ad2b7234fe1689fcb}\label{locator_8c_a651b4eec34e0ce0ad2b7234fe1689fcb}} 
\index{locator.c@{locator.c}!params@{params}}
\index{params@{params}!locator.c@{locator.c}}
\doxysubsubsection{\texorpdfstring{params}{params}}
{\footnotesize\ttfamily snd\+\_\+pcm\+\_\+hw\+\_\+params\+\_\+t$\ast$ params}

\mbox{\Hypertarget{locator_8c_a1f14db325606d8f825754cff1cc21123}\label{locator_8c_a1f14db325606d8f825754cff1cc21123}} 
\index{locator.c@{locator.c}!pcm\_bufsize@{pcm\_bufsize}}
\index{pcm\_bufsize@{pcm\_bufsize}!locator.c@{locator.c}}
\doxysubsubsection{\texorpdfstring{pcm\_bufsize}{pcm\_bufsize}}
{\footnotesize\ttfamily int pcm\+\_\+bufsize = 0}

\mbox{\Hypertarget{locator_8c_aa246ca2e7708de6457661f06ff4ecf8f}\label{locator_8c_aa246ca2e7708de6457661f06ff4ecf8f}} 
\index{locator.c@{locator.c}!right@{right}}
\index{right@{right}!locator.c@{locator.c}}
\doxysubsubsection{\texorpdfstring{right}{right}}
{\footnotesize\ttfamily signed int$\ast$ right}

Buffer for right mic. 

This buffer is read into when the multiplexer select is 1. \mbox{\Hypertarget{locator_8c_a1c086f81c095b0efd7a87ee29fc5ba7e}\label{locator_8c_a1c086f81c095b0efd7a87ee29fc5ba7e}} 
\index{locator.c@{locator.c}!sample\_rate@{sample\_rate}}
\index{sample\_rate@{sample\_rate}!locator.c@{locator.c}}
\doxysubsubsection{\texorpdfstring{sample\_rate}{sample\_rate}}
{\footnotesize\ttfamily unsigned int sample\+\_\+rate}

\mbox{\Hypertarget{locator_8c_a7afcac3447636c03934613716685bbc8}\label{locator_8c_a7afcac3447636c03934613716685bbc8}} 
\index{locator.c@{locator.c}!sel@{sel}}
\index{sel@{sel}!locator.c@{locator.c}}
\doxysubsubsection{\texorpdfstring{sel}{sel}}
{\footnotesize\ttfamily int sel}

\mbox{\Hypertarget{locator_8c_a195834fe831b25227f2ed54948dc06e9}\label{locator_8c_a195834fe831b25227f2ed54948dc06e9}} 
\index{locator.c@{locator.c}!top1@{top1}}
\index{top1@{top1}!locator.c@{locator.c}}
\doxysubsubsection{\texorpdfstring{top1}{top1}}
{\footnotesize\ttfamily signed int$\ast$ top1}

Buffer for top mic. 

This buffer, along with left is read into when the multiplexer select is 0. \mbox{\Hypertarget{locator_8c_aa489c260f2bf8edb93576e1d945fed13}\label{locator_8c_aa489c260f2bf8edb93576e1d945fed13}} 
\index{locator.c@{locator.c}!top2@{top2}}
\index{top2@{top2}!locator.c@{locator.c}}
\doxysubsubsection{\texorpdfstring{top2}{top2}}
{\footnotesize\ttfamily signed int$\ast$ top2}

Buffer for top mic. 

This buffer, along with right is read into when the multiplexer select is 1. \mbox{\Hypertarget{locator_8c_a81e715298ef2793d7133ced346aae6e5}\label{locator_8c_a81e715298ef2793d7133ced346aae6e5}} 
\index{locator.c@{locator.c}!zeroLeft@{zeroLeft}}
\index{zeroLeft@{zeroLeft}!locator.c@{locator.c}}
\doxysubsubsection{\texorpdfstring{zeroLeft}{zeroLeft}}
{\footnotesize\ttfamily int zero\+Left}

Index of zero crossing in left mic buffer. 

\mbox{\Hypertarget{locator_8c_a6803a267f65c0269820bd931dae3f2f2}\label{locator_8c_a6803a267f65c0269820bd931dae3f2f2}} 
\index{locator.c@{locator.c}!zeroRight@{zeroRight}}
\index{zeroRight@{zeroRight}!locator.c@{locator.c}}
\doxysubsubsection{\texorpdfstring{zeroRight}{zeroRight}}
{\footnotesize\ttfamily int zero\+Right}

Index of zero crossing in right mic buffer. 

\mbox{\Hypertarget{locator_8c_a4daf39371ce88e725afdddef077ad0da}\label{locator_8c_a4daf39371ce88e725afdddef077ad0da}} 
\index{locator.c@{locator.c}!zeroTop1@{zeroTop1}}
\index{zeroTop1@{zeroTop1}!locator.c@{locator.c}}
\doxysubsubsection{\texorpdfstring{zeroTop1}{zeroTop1}}
{\footnotesize\ttfamily int zero\+Top1}

Index of zero crossing in top1 mic buffer. 

\mbox{\Hypertarget{locator_8c_ab7af76e9f538eb8576c1435dccd847d1}\label{locator_8c_ab7af76e9f538eb8576c1435dccd847d1}} 
\index{locator.c@{locator.c}!zeroTop2@{zeroTop2}}
\index{zeroTop2@{zeroTop2}!locator.c@{locator.c}}
\doxysubsubsection{\texorpdfstring{zeroTop2}{zeroTop2}}
{\footnotesize\ttfamily int zero\+Top2}

Index of zero crossing in top2 mic buffer.

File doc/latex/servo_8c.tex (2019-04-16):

\hypertarget{servo_8c}{}\doxysection{servo.\+c File Reference}
\label{servo_8c}\index{servo.c@{servo.c}}
{\ttfamily \#include \char`\"{}servo.\+h\char`\"{}}\newline
{\ttfamily \#include $<$wiring\+Pi.\+h$>$}\newline
{\ttfamily \#include $<$stdlib.\+h$>$}\newline
{\ttfamily \#include $<$stdio.\+h$>$}\newline
\doxysubsection*{Macros}
\begin{DoxyCompactItemize}
\item 
\#define \mbox{\hyperlink{servo_8c_a9d71ebbfca932a711fc23aa5f78a3ed6}{T\+U\+R\+N\+M\+O\+T\+O\+R\+TO}}~\mbox{\hyperlink{servo_8h_ad20491cf5c1e75934f5d490a9b254e00}{turn\+Motor\+To}}
\end{DoxyCompactItemize}
\doxysubsection*{Functions}
\begin{DoxyCompactItemize}
\item 
void \mbox{\hyperlink{servo_8c_a9ea73d9b44445cd0f961ef72452b7ce2}{mock\+\_\+turn\+Motor\+To}} (int angle, int motor)
\item 
int \mbox{\hyperlink{servo_8c_a5adeec951f9dff5479c74d8a8a9ad4fd}{get\+Pwm\+Clk}} (int pwm\+Range)
\item 
int \mbox{\hyperlink{servo_8c_a9d197f8487cd224eed120cc78dc611fa}{get\+Pwm\+Value}} (int angle)
\item 
void \mbox{\hyperlink{servo_8c_ad20491cf5c1e75934f5d490a9b254e00}{turn\+Motor\+To}} (int angle, int motor)
\item 
void \mbox{\hyperlink{servo_8c_ab32c81b44ca8ff9817ca35c5bc04d750}{stop\+Motor}} (int pin)
\item 
void \mbox{\hyperlink{servo_8c_a5260da8b51f5d97f6cf2a9ba11d1aee1}{stop\+Motors}} ()
\begin{DoxyCompactList}\small\item\em Stops movement of both servos. \end{DoxyCompactList}\item 
void \mbox{\hyperlink{servo_8c_ab268235c450aa6cb5615779a1b0f5b28}{turn\+Motor\+By}} (int angle, int motor, int $\ast$curr)
\begin{DoxyCompactList}\small\item\em Turns a given motor by the specified angle in degrees. \end{DoxyCompactList}\item 
void \mbox{\hyperlink{servo_8c_a1c860ac83dd57815216ea7f9a7c190c7}{zero\+Azimuth}} (int $\ast$curr)
\item 
void \mbox{\hyperlink{servo_8c_a167c0bbab7d9bb43b16c49fd43046dcf}{zero\+Elevation}} (int $\ast$curr)
\item 
void \mbox{\hyperlink{servo_8c_a7a63f5a5a10bf73d98ae5ff7efcdd57e}{zero\+Motors}} (int $\ast$\mbox{\hyperlink{locator_8c_af15ce0e091b409de25694109f11f484b}{az\+\_\+curr}}, int $\ast$\mbox{\hyperlink{locator_8c_adfd48dc66211fce52f7d14f4e780ae02}{el\+\_\+curr}})
\begin{DoxyCompactList}\small\item\em Brings both servos to their 0 position, i.\+e. \end{DoxyCompactList}\item 
void \mbox{\hyperlink{servo_8c_a0b4159671b6e3c2818e560def5da3dd7}{pwm\+Setup}} ()
\begin{DoxyCompactList}\small\item\em Sets up P\+WM control for the servo motors. \end{DoxyCompactList}\item 
void \mbox{\hyperlink{servo_8c_ab7037f4d33836bb66b1e31183dc70ec6}{laser\+On}} ()
\begin{DoxyCompactList}\small\item\em Turns on the front L\+ED. \end{DoxyCompactList}\item 
void \mbox{\hyperlink{servo_8c_a9c33a84099f27158bf60c78f7d2353d6}{laser\+Off}} ()
\begin{DoxyCompactList}\small\item\em Turns off the front L\+ED. \end{DoxyCompactList}\end{DoxyCompactItemize}

\doxysubsection{Macro Definition Documentation}
\mbox{\Hypertarget{servo_8c_a9d71ebbfca932a711fc23aa5f78a3ed6}\label{servo_8c_a9d71ebbfca932a711fc23aa5f78a3ed6}} 
\index{servo.c@{servo.c}!TURNMOTORTO@{TURNMOTORTO}}
\index{TURNMOTORTO@{TURNMOTORTO}!servo.c@{servo.c}}
\doxysubsubsection{\texorpdfstring{TURNMOTORTO}{TURNMOTORTO}}
{\footnotesize\ttfamily \#define T\+U\+R\+N\+M\+O\+T\+O\+R\+TO~\mbox{\hyperlink{servo_8h_ad20491cf5c1e75934f5d490a9b254e00}{turn\+Motor\+To}}}

\doxysubsection{Function Documentation}
\mbox{\Hypertarget{servo_8c_a5adeec951f9dff5479c74d8a8a9ad4fd}\label{servo_8c_a5adeec951f9dff5479c74d8a8a9ad4fd}} 
\index{servo.c@{servo.c}!getPwmClk@{getPwmClk}}
\index{getPwmClk@{getPwmClk}!servo.c@{servo.c}}
\doxysubsubsection{\texorpdfstring{getPwmClk()}{getPwmClk()}}
{\footnotesize\ttfamily int get\+Pwm\+Clk (\begin{DoxyParamCaption}\item[{int}]{pwm\+Range }\end{DoxyParamCaption})}

\mbox{\Hypertarget{servo_8c_a9d197f8487cd224eed120cc78dc611fa}\label{servo_8c_a9d197f8487cd224eed120cc78dc611fa}} 
\index{servo.c@{servo.c}!getPwmValue@{getPwmValue}}
\index{getPwmValue@{getPwmValue}!servo.c@{servo.c}}
\doxysubsubsection{\texorpdfstring{getPwmValue()}{getPwmValue()}}
{\footnotesize\ttfamily int get\+Pwm\+Value (\begin{DoxyParamCaption}\item[{int}]{angle }\end{DoxyParamCaption})}

\mbox{\Hypertarget{servo_8c_a9c33a84099f27158bf60c78f7d2353d6}\label{servo_8c_a9c33a84099f27158bf60c78f7d2353d6}} 
\index{servo.c@{servo.c}!laserOff@{laserOff}}
\index{laserOff@{laserOff}!servo.c@{servo.c}}
\doxysubsubsection{\texorpdfstring{laserOff()}{laserOff()}}
{\footnotesize\ttfamily void laser\+Off (\begin{DoxyParamCaption}{ }\end{DoxyParamCaption})}

Turns off the front L\+ED. 

\mbox{\Hypertarget{servo_8c_ab7037f4d33836bb66b1e31183dc70ec6}\label{servo_8c_ab7037f4d33836bb66b1e31183dc70ec6}} 
\index{servo.c@{servo.c}!laserOn@{laserOn}}
\index{laserOn@{laserOn}!servo.c@{servo.c}}
\doxysubsubsection{\texorpdfstring{laserOn()}{laserOn()}}
{\footnotesize\ttfamily void laser\+On (\begin{DoxyParamCaption}{ }\end{DoxyParamCaption})}

Turns on the front L\+ED. 

\mbox{\Hypertarget{servo_8c_a9ea73d9b44445cd0f961ef72452b7ce2}\label{servo_8c_a9ea73d9b44445cd0f961ef72452b7ce2}} 
\index{servo.c@{servo.c}!mock\_turnMotorTo@{mock\_turnMotorTo}}
\index{mock\_turnMotorTo@{mock\_turnMotorTo}!servo.c@{servo.c}}
\doxysubsubsection{\texorpdfstring{mock\_turnMotorTo()}{mock\_turnMotorTo()}}
{\footnotesize\ttfamily void mock\+\_\+turn\+Motor\+To (\begin{DoxyParamCaption}\item[{int}]{angle,  }\item[{int}]{motor }\end{DoxyParamCaption})}

\mbox{\Hypertarget{servo_8c_a0b4159671b6e3c2818e560def5da3dd7}\label{servo_8c_a0b4159671b6e3c2818e560def5da3dd7}} 
\index{servo.c@{servo.c}!pwmSetup@{pwmSetup}}
\index{pwmSetup@{pwmSetup}!servo.c@{servo.c}}
\doxysubsubsection{\texorpdfstring{pwmSetup()}{pwmSetup()}}
{\footnotesize\ttfamily void pwm\+Setup (\begin{DoxyParamCaption}{ }\end{DoxyParamCaption})}

Sets up P\+WM control for the servo motors. 

\mbox{\Hypertarget{servo_8c_ab32c81b44ca8ff9817ca35c5bc04d750}\label{servo_8c_ab32c81b44ca8ff9817ca35c5bc04d750}} 
\index{servo.c@{servo.c}!stopMotor@{stopMotor}}
\index{stopMotor@{stopMotor}!servo.c@{servo.c}}
\doxysubsubsection{\texorpdfstring{stopMotor()}{stopMotor()}}
{\footnotesize\ttfamily void stop\+Motor (\begin{DoxyParamCaption}\item[{int}]{pin }\end{DoxyParamCaption})}

\mbox{\Hypertarget{servo_8c_a5260da8b51f5d97f6cf2a9ba11d1aee1}\label{servo_8c_a5260da8b51f5d97f6cf2a9ba11d1aee1}} 
\index{servo.c@{servo.c}!stopMotors@{stopMotors}}
\index{stopMotors@{stopMotors}!servo.c@{servo.c}}
\doxysubsubsection{\texorpdfstring{stopMotors()}{stopMotors()}}
{\footnotesize\ttfamily void stop\+Motors (\begin{DoxyParamCaption}{ }\end{DoxyParamCaption})}

Stops movement of both servos. 

\mbox{\Hypertarget{servo_8c_ab268235c450aa6cb5615779a1b0f5b28}\label{servo_8c_ab268235c450aa6cb5615779a1b0f5b28}} 
\index{servo.c@{servo.c}!turnMotorBy@{turnMotorBy}}
\index{turnMotorBy@{turnMotorBy}!servo.c@{servo.c}}
\doxysubsubsection{\texorpdfstring{turnMotorBy()}{turnMotorBy()}}
{\footnotesize\ttfamily void turn\+Motor\+By (\begin{DoxyParamCaption}\item[{int}]{angle,  }\item[{int}]{motor,  }\item[{int $\ast$}]{curr }\end{DoxyParamCaption})}

Turns a given motor by the specified angle in degrees. 

Prevents movements of the servos at their angular limits so as to avoid damage 
\begin{DoxyParams}{Parameters}
{\em angle} & The angle by which the motor should turn. \\
\hline
{\em motor} & An integer that distiguishes between the azimuthal or elevation servo. \\
\hline
{\em curr} & The current angular position of the servo \\
\hline
\end{DoxyParams}
\begin{DoxySeeAlso}{See also}
\mbox{\hyperlink{servo_8h_a101a400582c692f5f5014eec55a49a30}{A\+Z\+I\+M\+U\+TH}} 

\mbox{\hyperlink{servo_8h_a3e4d4fc6ada25dbf92510809adde0263}{E\+L\+E\+V\+A\+T\+I\+ON}} 
\end{DoxySeeAlso}
\mbox{\Hypertarget{servo_8c_ad20491cf5c1e75934f5d490a9b254e00}\label{servo_8c_ad20491cf5c1e75934f5d490a9b254e00}} 
\index{servo.c@{servo.c}!turnMotorTo@{turnMotorTo}}
\index{turnMotorTo@{turnMotorTo}!servo.c@{servo.c}}
\doxysubsubsection{\texorpdfstring{turnMotorTo()}{turnMotorTo()}}
{\footnotesize\ttfamily void turn\+Motor\+To (\begin{DoxyParamCaption}\item[{int}]{angle,  }\item[{int}]{motor }\end{DoxyParamCaption})}

\mbox{\Hypertarget{servo_8c_a1c860ac83dd57815216ea7f9a7c190c7}\label{servo_8c_a1c860ac83dd57815216ea7f9a7c190c7}} 
\index{servo.c@{servo.c}!zeroAzimuth@{zeroAzimuth}}
\index{zeroAzimuth@{zeroAzimuth}!servo.c@{servo.c}}
\doxysubsubsection{\texorpdfstring{zeroAzimuth()}{zeroAzimuth()}}
{\footnotesize\ttfamily void zero\+Azimuth (\begin{DoxyParamCaption}\item[{int $\ast$}]{curr }\end{DoxyParamCaption})}

\mbox{\Hypertarget{servo_8c_a167c0bbab7d9bb43b16c49fd43046dcf}\label{servo_8c_a167c0bbab7d9bb43b16c49fd43046dcf}} 
\index{servo.c@{servo.c}!zeroElevation@{zeroElevation}}
\index{zeroElevation@{zeroElevation}!servo.c@{servo.c}}
\doxysubsubsection{\texorpdfstring{zeroElevation()}{zeroElevation()}}
{\footnotesize\ttfamily void zero\+Elevation (\begin{DoxyParamCaption}\item[{int $\ast$}]{curr }\end{DoxyParamCaption})}

\mbox{\Hypertarget{servo_8c_a7a63f5a5a10bf73d98ae5ff7efcdd57e}\label{servo_8c_a7a63f5a5a10bf73d98ae5ff7efcdd57e}} 
\index{servo.c@{servo.c}!zeroMotors@{zeroMotors}}
\index{zeroMotors@{zeroMotors}!servo.c@{servo.c}}
\doxysubsubsection{\texorpdfstring{zeroMotors()}{zeroMotors()}}
{\footnotesize\ttfamily void zero\+Motors (\begin{DoxyParamCaption}\item[{int $\ast$}]{az\+\_\+curr,  }\item[{int $\ast$}]{el\+\_\+curr }\end{DoxyParamCaption})}

Brings both servos to their 0 position, i.\+e. 

facing straight ahead. 
\begin{DoxyParams}{Parameters}
{\em az\+\_\+curr} & current position of azimuthal motor (degrees) \\
\hline
{\em el\+\_\+curr} & current position of elevation motor (degrees) \\
\hline
\end{DoxyParams}

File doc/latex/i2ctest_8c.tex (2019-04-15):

\hypertarget{i2ctest_8c}{}\doxysection{i2ctest.\+c File Reference}
\label{i2ctest_8c}\index{i2ctest.c@{i2ctest.c}}
{\ttfamily \#include $<$stdio.\+h$>$}\newline
{\ttfamily \#include $<$wiring\+Pi\+I2\+C.\+h$>$}\newline
{\ttfamily \#include $<$time.\+h$>$}\newline
\doxysubsection*{Functions}
\begin{DoxyCompactItemize}
\item 
int \mbox{\hyperlink{i2ctest_8c_ae66f6b31b5ad750f1fe042a706a4e3d4}{main}} ()
\end{DoxyCompactItemize}

\doxysubsection{Function Documentation}
\mbox{\Hypertarget{i2ctest_8c_ae66f6b31b5ad750f1fe042a706a4e3d4}\label{i2ctest_8c_ae66f6b31b5ad750f1fe042a706a4e3d4}} 
\index{i2ctest.c@{i2ctest.c}!main@{main}}
\index{main@{main}!i2ctest.c@{i2ctest.c}}
\doxysubsubsection{\texorpdfstring{main()}{main()}}
{\footnotesize\ttfamily int main (\begin{DoxyParamCaption}{ }\end{DoxyParamCaption})}

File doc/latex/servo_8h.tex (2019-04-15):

\hypertarget{servo_8h}{}\doxysection{servo.\+h File Reference}
\label{servo_8h}\index{servo.h@{servo.h}}
\doxysubsection*{Macros}
\begin{DoxyCompactItemize}
\item 
\#define \mbox{\hyperlink{servo_8h_a7ec8393e9445109104fd54119e06fc08}{L\+A\+S\+ER}}~22
\begin{DoxyCompactList}\small\item\em wiring\+Pi pin connected to L\+ED. \end{DoxyCompactList}\item 
\#define \mbox{\hyperlink{servo_8h_a3e4d4fc6ada25dbf92510809adde0263}{E\+L\+E\+V\+A\+T\+I\+ON}}~23
\begin{DoxyCompactList}\small\item\em wiring\+Pi pin connected to top servo. \end{DoxyCompactList}\item 
\#define \mbox{\hyperlink{servo_8h_a101a400582c692f5f5014eec55a49a30}{A\+Z\+I\+M\+U\+TH}}~26
\begin{DoxyCompactList}\small\item\em wiring\+Pi pin connected to bottom servo. \end{DoxyCompactList}\item 
\#define \mbox{\hyperlink{servo_8h_a5361356710fb7819fc6c9c3712d10db6}{B\+A\+S\+E\+\_\+\+C\+LK}}~19200000
\begin{DoxyCompactList}\small\item\em Raspberry Pi base clock frequency (Hz). \end{DoxyCompactList}\item 
\#define \mbox{\hyperlink{servo_8h_a76fe84d83b8d236bd4f0d20d7e2ed06f}{P\+W\+M\+\_\+\+F\+R\+EQ}}~50
\begin{DoxyCompactList}\small\item\em Desired P\+WM frequency (Hz). \end{DoxyCompactList}\item 
\#define \mbox{\hyperlink{servo_8h_a48ea2ccd8887eb8389b8043bf620d1a3}{P\+W\+M\+R\+NG}}~2000
\begin{DoxyCompactList}\small\item\em Range of P\+WM period. \end{DoxyCompactList}\item 
\#define \mbox{\hyperlink{servo_8h_ae23f58b84e7575a296229c23ccb8b567}{A\+Z\+\_\+\+M\+AX}}~90
\begin{DoxyCompactList}\small\item\em Maximum azimuthal angle (degrees). \end{DoxyCompactList}\item 
\#define \mbox{\hyperlink{servo_8h_a599ca6840731539d1b83e7eda09f5000}{A\+Z\+\_\+\+M\+IN}}~-\/90
\begin{DoxyCompactList}\small\item\em Minimum azimuthal angle (degrees). \end{DoxyCompactList}\item 
\#define \mbox{\hyperlink{servo_8h_a97f175fa73362fa14b84cfead6088124}{E\+L\+\_\+\+M\+AX}}~70
\begin{DoxyCompactList}\small\item\em Maximum elevation angle (degrees). \end{DoxyCompactList}\item 
\#define \mbox{\hyperlink{servo_8h_ae6a195e81a9b69d16111a762b146b14c}{E\+L\+\_\+\+M\+IN}}~-\/35
\begin{DoxyCompactList}\small\item\em Minimum elevation angle (degrees). \end{DoxyCompactList}\item 
\#define \mbox{\hyperlink{servo_8h_a62249e384b997229a3e2ae74ade334e2}{D\+E\+L\+AY}}~250
\begin{DoxyCompactList}\small\item\em Servo delay (milliseconds). \end{DoxyCompactList}\end{DoxyCompactItemize}
\doxysubsection*{Functions}
\begin{DoxyCompactItemize}
\item 
void \mbox{\hyperlink{servo_8h_a0b4159671b6e3c2818e560def5da3dd7}{pwm\+Setup}} ()
\begin{DoxyCompactList}\small\item\em Sets up P\+WM control for the servo motors. \end{DoxyCompactList}\item 
void \mbox{\hyperlink{servo_8h_ab7037f4d33836bb66b1e31183dc70ec6}{laser\+On}} ()
\begin{DoxyCompactList}\small\item\em Turns on the front L\+ED. \end{DoxyCompactList}\item 
void \mbox{\hyperlink{servo_8h_a9c33a84099f27158bf60c78f7d2353d6}{laser\+Off}} ()
\begin{DoxyCompactList}\small\item\em Turns off the front L\+ED. \end{DoxyCompactList}\item 
void \mbox{\hyperlink{servo_8h_a5260da8b51f5d97f6cf2a9ba11d1aee1}{stop\+Motors}} ()
\begin{DoxyCompactList}\small\item\em Stops movement of both servos. \end{DoxyCompactList}\item 
void \mbox{\hyperlink{servo_8h_a7a63f5a5a10bf73d98ae5ff7efcdd57e}{zero\+Motors}} (int $\ast$\mbox{\hyperlink{locator_8c_af15ce0e091b409de25694109f11f484b}{az\+\_\+curr}}, int $\ast$\mbox{\hyperlink{locator_8c_adfd48dc66211fce52f7d14f4e780ae02}{el\+\_\+curr}})
\begin{DoxyCompactList}\small\item\em Brings both servos to their 0 position, i.\+e. \end{DoxyCompactList}\item 
void \mbox{\hyperlink{servo_8h_ab268235c450aa6cb5615779a1b0f5b28}{turn\+Motor\+By}} (int angle, int motor, int $\ast$curr)
\begin{DoxyCompactList}\small\item\em Turns a given motor by the specified angle in degrees. \end{DoxyCompactList}\item 
void \mbox{\hyperlink{servo_8h_a1c860ac83dd57815216ea7f9a7c190c7}{zero\+Azimuth}} (int $\ast$curr)
\item 
void \mbox{\hyperlink{servo_8h_a167c0bbab7d9bb43b16c49fd43046dcf}{zero\+Elevation}} (int $\ast$curr)
\item 
int \mbox{\hyperlink{servo_8h_a5adeec951f9dff5479c74d8a8a9ad4fd}{get\+Pwm\+Clk}} (int pwm\+Range)
\item 
int \mbox{\hyperlink{servo_8h_a9d197f8487cd224eed120cc78dc611fa}{get\+Pwm\+Value}} (int angle)
\item 
void \mbox{\hyperlink{servo_8h_ad20491cf5c1e75934f5d490a9b254e00}{turn\+Motor\+To}} (int angle, int motor)
\item 
void \mbox{\hyperlink{servo_8h_ac51721527479fe4e5cc6a1192116a770}{stop\+Motor}} (int motor)
\end{DoxyCompactItemize}

\doxysubsection{Macro Definition Documentation}
\mbox{\Hypertarget{servo_8h_ae23f58b84e7575a296229c23ccb8b567}\label{servo_8h_ae23f58b84e7575a296229c23ccb8b567}} 
\index{servo.h@{servo.h}!AZ\_MAX@{AZ\_MAX}}
\index{AZ\_MAX@{AZ\_MAX}!servo.h@{servo.h}}
\doxysubsubsection{\texorpdfstring{AZ\_MAX}{AZ\_MAX}}
{\footnotesize\ttfamily \#define A\+Z\+\_\+\+M\+AX~90}

Maximum azimuthal angle (degrees). 

Used in limiting range of motion to prevent damage. \mbox{\Hypertarget{servo_8h_a599ca6840731539d1b83e7eda09f5000}\label{servo_8h_a599ca6840731539d1b83e7eda09f5000}} 
\index{servo.h@{servo.h}!AZ\_MIN@{AZ\_MIN}}
\index{AZ\_MIN@{AZ\_MIN}!servo.h@{servo.h}}
\doxysubsubsection{\texorpdfstring{AZ\_MIN}{AZ\_MIN}}
{\footnotesize\ttfamily \#define A\+Z\+\_\+\+M\+IN~-\/90}

Minimum azimuthal angle (degrees). 

Used in limiting range of motion to prevent damage. \mbox{\Hypertarget{servo_8h_a101a400582c692f5f5014eec55a49a30}\label{servo_8h_a101a400582c692f5f5014eec55a49a30}} 
\index{servo.h@{servo.h}!AZIMUTH@{AZIMUTH}}
\index{AZIMUTH@{AZIMUTH}!servo.h@{servo.h}}
\doxysubsubsection{\texorpdfstring{AZIMUTH}{AZIMUTH}}
{\footnotesize\ttfamily \#define A\+Z\+I\+M\+U\+TH~26}

wiring\+Pi pin connected to bottom servo. 

\mbox{\Hypertarget{servo_8h_a5361356710fb7819fc6c9c3712d10db6}\label{servo_8h_a5361356710fb7819fc6c9c3712d10db6}} 
\index{servo.h@{servo.h}!BASE\_CLK@{BASE\_CLK}}
\index{BASE\_CLK@{BASE\_CLK}!servo.h@{servo.h}}
\doxysubsubsection{\texorpdfstring{BASE\_CLK}{BASE\_CLK}}
{\footnotesize\ttfamily \#define B\+A\+S\+E\+\_\+\+C\+LK~19200000}

Raspberry Pi base clock frequency (Hz). 

\mbox{\Hypertarget{servo_8h_a62249e384b997229a3e2ae74ade334e2}\label{servo_8h_a62249e384b997229a3e2ae74ade334e2}} 
\index{servo.h@{servo.h}!DELAY@{DELAY}}
\index{DELAY@{DELAY}!servo.h@{servo.h}}
\doxysubsubsection{\texorpdfstring{DELAY}{DELAY}}
{\footnotesize\ttfamily \#define D\+E\+L\+AY~250}

Servo delay (milliseconds). 

Used in preventing jitter. \mbox{\Hypertarget{servo_8h_a97f175fa73362fa14b84cfead6088124}\label{servo_8h_a97f175fa73362fa14b84cfead6088124}} 
\index{servo.h@{servo.h}!EL\_MAX@{EL\_MAX}}
\index{EL\_MAX@{EL\_MAX}!servo.h@{servo.h}}
\doxysubsubsection{\texorpdfstring{EL\_MAX}{EL\_MAX}}
{\footnotesize\ttfamily \#define E\+L\+\_\+\+M\+AX~70}

Maximum elevation angle (degrees). 

Used in limiting range of motion to prevent damage. \mbox{\Hypertarget{servo_8h_ae6a195e81a9b69d16111a762b146b14c}\label{servo_8h_ae6a195e81a9b69d16111a762b146b14c}} 
\index{servo.h@{servo.h}!EL\_MIN@{EL\_MIN}}
\index{EL\_MIN@{EL\_MIN}!servo.h@{servo.h}}
\doxysubsubsection{\texorpdfstring{EL\_MIN}{EL\_MIN}}
{\footnotesize\ttfamily \#define E\+L\+\_\+\+M\+IN~-\/35}

Minimum elevation angle (degrees). 

Used in limiting range of motion to prevent damage. \mbox{\Hypertarget{servo_8h_a3e4d4fc6ada25dbf92510809adde0263}\label{servo_8h_a3e4d4fc6ada25dbf92510809adde0263}} 
\index{servo.h@{servo.h}!ELEVATION@{ELEVATION}}
\index{ELEVATION@{ELEVATION}!servo.h@{servo.h}}
\doxysubsubsection{\texorpdfstring{ELEVATION}{ELEVATION}}
{\footnotesize\ttfamily \#define E\+L\+E\+V\+A\+T\+I\+ON~23}

wiring\+Pi pin connected to top servo. 

\mbox{\Hypertarget{servo_8h_a7ec8393e9445109104fd54119e06fc08}\label{servo_8h_a7ec8393e9445109104fd54119e06fc08}} 
\index{servo.h@{servo.h}!LASER@{LASER}}
\index{LASER@{LASER}!servo.h@{servo.h}}
\doxysubsubsection{\texorpdfstring{LASER}{LASER}}
{\footnotesize\ttfamily \#define L\+A\+S\+ER~22}

wiring\+Pi pin connected to L\+ED. 

\mbox{\Hypertarget{servo_8h_a76fe84d83b8d236bd4f0d20d7e2ed06f}\label{servo_8h_a76fe84d83b8d236bd4f0d20d7e2ed06f}} 
\index{servo.h@{servo.h}!PWM\_FREQ@{PWM\_FREQ}}
\index{PWM\_FREQ@{PWM\_FREQ}!servo.h@{servo.h}}
\doxysubsubsection{\texorpdfstring{PWM\_FREQ}{PWM\_FREQ}}
{\footnotesize\ttfamily \#define P\+W\+M\+\_\+\+F\+R\+EQ~50}

Desired P\+WM frequency (Hz). 

\mbox{\Hypertarget{servo_8h_a48ea2ccd8887eb8389b8043bf620d1a3}\label{servo_8h_a48ea2ccd8887eb8389b8043bf620d1a3}} 
\index{servo.h@{servo.h}!PWMRNG@{PWMRNG}}
\index{PWMRNG@{PWMRNG}!servo.h@{servo.h}}
\doxysubsubsection{\texorpdfstring{PWMRNG}{PWMRNG}}
{\footnotesize\ttfamily \#define P\+W\+M\+R\+NG~2000}

Range of P\+WM period. 

\doxysubsection{Function Documentation}
\mbox{\Hypertarget{servo_8h_a5adeec951f9dff5479c74d8a8a9ad4fd}\label{servo_8h_a5adeec951f9dff5479c74d8a8a9ad4fd}} 
\index{servo.h@{servo.h}!getPwmClk@{getPwmClk}}
\index{getPwmClk@{getPwmClk}!servo.h@{servo.h}}
\doxysubsubsection{\texorpdfstring{getPwmClk()}{getPwmClk()}}
{\footnotesize\ttfamily int get\+Pwm\+Clk (\begin{DoxyParamCaption}\item[{int}]{pwm\+Range }\end{DoxyParamCaption})}

\mbox{\Hypertarget{servo_8h_a9d197f8487cd224eed120cc78dc611fa}\label{servo_8h_a9d197f8487cd224eed120cc78dc611fa}} 
\index{servo.h@{servo.h}!getPwmValue@{getPwmValue}}
\index{getPwmValue@{getPwmValue}!servo.h@{servo.h}}
\doxysubsubsection{\texorpdfstring{getPwmValue()}{getPwmValue()}}
{\footnotesize\ttfamily int get\+Pwm\+Value (\begin{DoxyParamCaption}\item[{int}]{angle }\end{DoxyParamCaption})}

\mbox{\Hypertarget{servo_8h_a9c33a84099f27158bf60c78f7d2353d6}\label{servo_8h_a9c33a84099f27158bf60c78f7d2353d6}} 
\index{servo.h@{servo.h}!laserOff@{laserOff}}
\index{laserOff@{laserOff}!servo.h@{servo.h}}
\doxysubsubsection{\texorpdfstring{laserOff()}{laserOff()}}
{\footnotesize\ttfamily void laser\+Off (\begin{DoxyParamCaption}{ }\end{DoxyParamCaption})}

Turns off the front L\+ED. 

\mbox{\Hypertarget{servo_8h_ab7037f4d33836bb66b1e31183dc70ec6}\label{servo_8h_ab7037f4d33836bb66b1e31183dc70ec6}} 
\index{servo.h@{servo.h}!laserOn@{laserOn}}
\index{laserOn@{laserOn}!servo.h@{servo.h}}
\doxysubsubsection{\texorpdfstring{laserOn()}{laserOn()}}
{\footnotesize\ttfamily void laser\+On (\begin{DoxyParamCaption}{ }\end{DoxyParamCaption})}

Turns on the front L\+ED. 

\mbox{\Hypertarget{servo_8h_a0b4159671b6e3c2818e560def5da3dd7}\label{servo_8h_a0b4159671b6e3c2818e560def5da3dd7}} 
\index{servo.h@{servo.h}!pwmSetup@{pwmSetup}}
\index{pwmSetup@{pwmSetup}!servo.h@{servo.h}}
\doxysubsubsection{\texorpdfstring{pwmSetup()}{pwmSetup()}}
{\footnotesize\ttfamily void pwm\+Setup (\begin{DoxyParamCaption}{ }\end{DoxyParamCaption})}

Sets up P\+WM control for the servo motors. 

\mbox{\Hypertarget{servo_8h_ac51721527479fe4e5cc6a1192116a770}\label{servo_8h_ac51721527479fe4e5cc6a1192116a770}} 
\index{servo.h@{servo.h}!stopMotor@{stopMotor}}
\index{stopMotor@{stopMotor}!servo.h@{servo.h}}
\doxysubsubsection{\texorpdfstring{stopMotor()}{stopMotor()}}
{\footnotesize\ttfamily void stop\+Motor (\begin{DoxyParamCaption}\item[{int}]{motor }\end{DoxyParamCaption})}

\mbox{\Hypertarget{servo_8h_a5260da8b51f5d97f6cf2a9ba11d1aee1}\label{servo_8h_a5260da8b51f5d97f6cf2a9ba11d1aee1}} 
\index{servo.h@{servo.h}!stopMotors@{stopMotors}}
\index{stopMotors@{stopMotors}!servo.h@{servo.h}}
\doxysubsubsection{\texorpdfstring{stopMotors()}{stopMotors()}}
{\footnotesize\ttfamily void stop\+Motors (\begin{DoxyParamCaption}{ }\end{DoxyParamCaption})}

Stops movement of both servos. 

\mbox{\Hypertarget{servo_8h_ab268235c450aa6cb5615779a1b0f5b28}\label{servo_8h_ab268235c450aa6cb5615779a1b0f5b28}} 
\index{servo.h@{servo.h}!turnMotorBy@{turnMotorBy}}
\index{turnMotorBy@{turnMotorBy}!servo.h@{servo.h}}
\doxysubsubsection{\texorpdfstring{turnMotorBy()}{turnMotorBy()}}
{\footnotesize\ttfamily void turn\+Motor\+By (\begin{DoxyParamCaption}\item[{int}]{angle,  }\item[{int}]{motor,  }\item[{int $\ast$}]{curr }\end{DoxyParamCaption})}

Turns a given motor by the specified angle in degrees. 

Prevents movements of the servos at their angular limits so as to avoid damage 
\begin{DoxyParams}{Parameters}
{\em angle} & The angle by which the motor should turn. \\
\hline
{\em motor} & An integer that distiguishes between the azimuthal or elevation servo. \\
\hline
{\em curr} & The current angular position of the servo \\
\hline
\end{DoxyParams}
\begin{DoxySeeAlso}{See also}
\mbox{\hyperlink{servo_8h_a101a400582c692f5f5014eec55a49a30}{A\+Z\+I\+M\+U\+TH}} 

\mbox{\hyperlink{servo_8h_a3e4d4fc6ada25dbf92510809adde0263}{E\+L\+E\+V\+A\+T\+I\+ON}} 
\end{DoxySeeAlso}
\mbox{\Hypertarget{servo_8h_ad20491cf5c1e75934f5d490a9b254e00}\label{servo_8h_ad20491cf5c1e75934f5d490a9b254e00}} 
\index{servo.h@{servo.h}!turnMotorTo@{turnMotorTo}}
\index{turnMotorTo@{turnMotorTo}!servo.h@{servo.h}}
\doxysubsubsection{\texorpdfstring{turnMotorTo()}{turnMotorTo()}}
{\footnotesize\ttfamily void turn\+Motor\+To (\begin{DoxyParamCaption}\item[{int}]{angle,  }\item[{int}]{motor }\end{DoxyParamCaption})}

\mbox{\Hypertarget{servo_8h_a1c860ac83dd57815216ea7f9a7c190c7}\label{servo_8h_a1c860ac83dd57815216ea7f9a7c190c7}} 
\index{servo.h@{servo.h}!zeroAzimuth@{zeroAzimuth}}
\index{zeroAzimuth@{zeroAzimuth}!servo.h@{servo.h}}
\doxysubsubsection{\texorpdfstring{zeroAzimuth()}{zeroAzimuth()}}
{\footnotesize\ttfamily void zero\+Azimuth (\begin{DoxyParamCaption}\item[{int $\ast$}]{curr }\end{DoxyParamCaption})}

\mbox{\Hypertarget{servo_8h_a167c0bbab7d9bb43b16c49fd43046dcf}\label{servo_8h_a167c0bbab7d9bb43b16c49fd43046dcf}} 
\index{servo.h@{servo.h}!zeroElevation@{zeroElevation}}
\index{zeroElevation@{zeroElevation}!servo.h@{servo.h}}
\doxysubsubsection{\texorpdfstring{zeroElevation()}{zeroElevation()}}
{\footnotesize\ttfamily void zero\+Elevation (\begin{DoxyParamCaption}\item[{int $\ast$}]{curr }\end{DoxyParamCaption})}

\mbox{\Hypertarget{servo_8h_a7a63f5a5a10bf73d98ae5ff7efcdd57e}\label{servo_8h_a7a63f5a5a10bf73d98ae5ff7efcdd57e}} 
\index{servo.h@{servo.h}!zeroMotors@{zeroMotors}}
\index{zeroMotors@{zeroMotors}!servo.h@{servo.h}}
\doxysubsubsection{\texorpdfstring{zeroMotors()}{zeroMotors()}}
{\footnotesize\ttfamily void zero\+Motors (\begin{DoxyParamCaption}\item[{int $\ast$}]{az\+\_\+curr,  }\item[{int $\ast$}]{el\+\_\+curr }\end{DoxyParamCaption})}

Brings both servos to their 0 position, i.\+e. 

facing straight ahead. 
\begin{DoxyParams}{Parameters}
{\em az\+\_\+curr} & current position of azimuthal motor (degrees) \\
\hline
{\em el\+\_\+curr} & current position of elevation motor (degrees) \\
\hline
\end{DoxyParams}

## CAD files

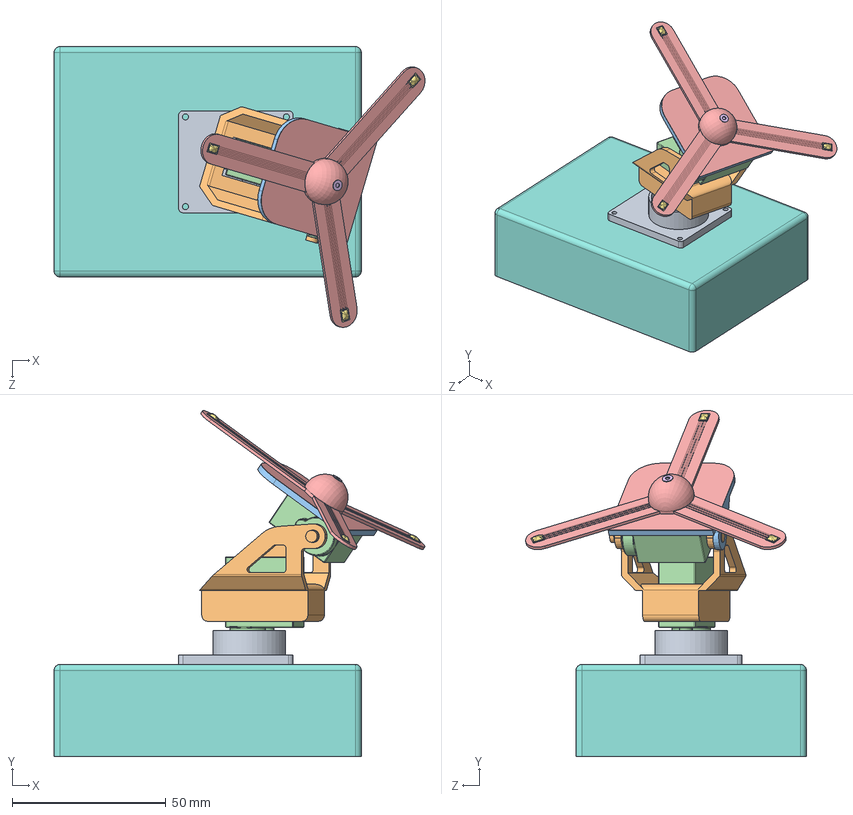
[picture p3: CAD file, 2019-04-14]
img/CAD/Designs/Gimbal assembly.SLDASM
120.7 x 112.6 x 91.4 mm
Gimbal Base
Gimbal mid
Gimbal top
motor x 2
head
laser led
microphone x 3

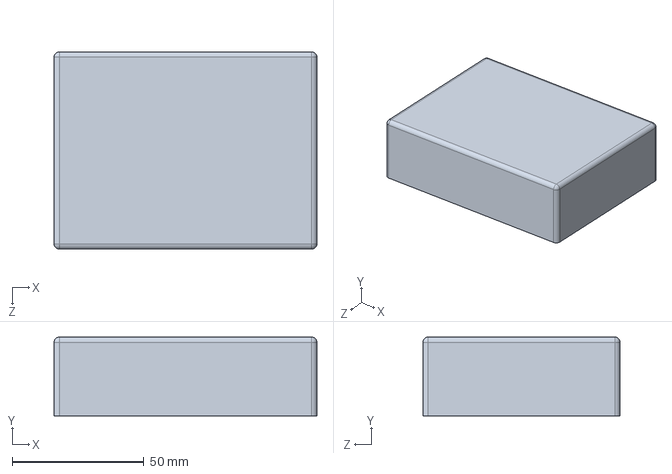
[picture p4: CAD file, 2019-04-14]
img/CAD/Designs/box.SLDPRT
100.0 x 30.0 x 75.0 mm

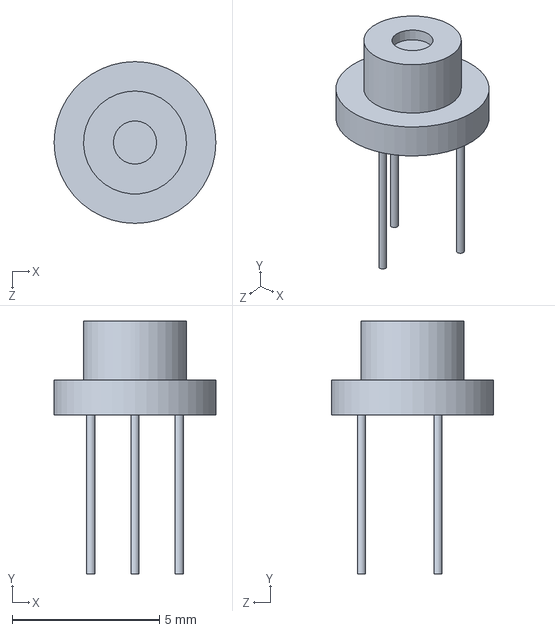
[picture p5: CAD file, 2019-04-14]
img/CAD/Designs/laser led.SLDPRT
5.50 x 8.60 x 5.50 mm

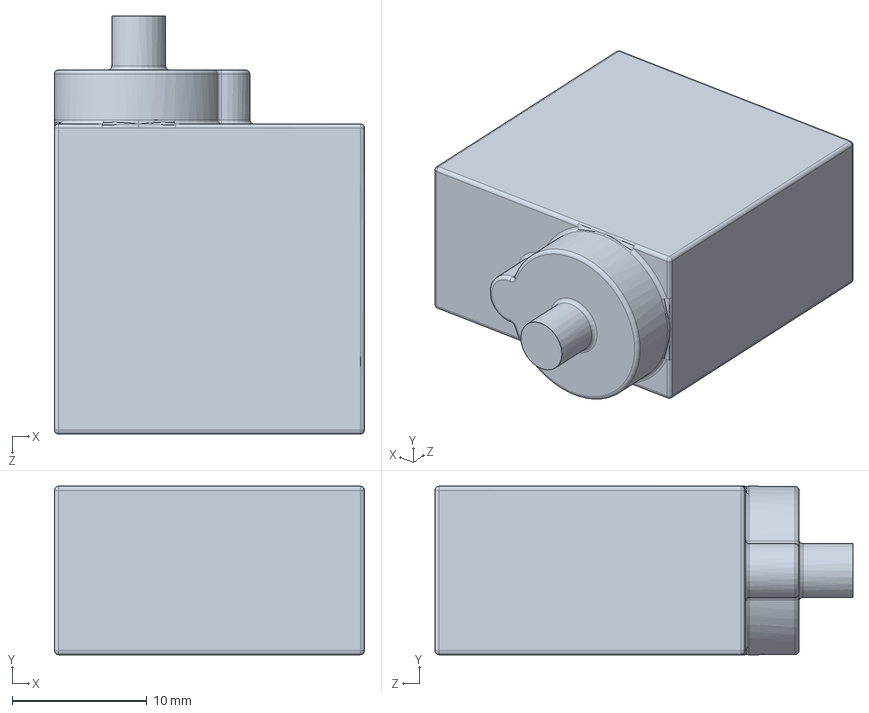
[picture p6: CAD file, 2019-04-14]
img/CAD/Designs/motor.SLDPRT
23.0 x 12.5 x 31.0 mm

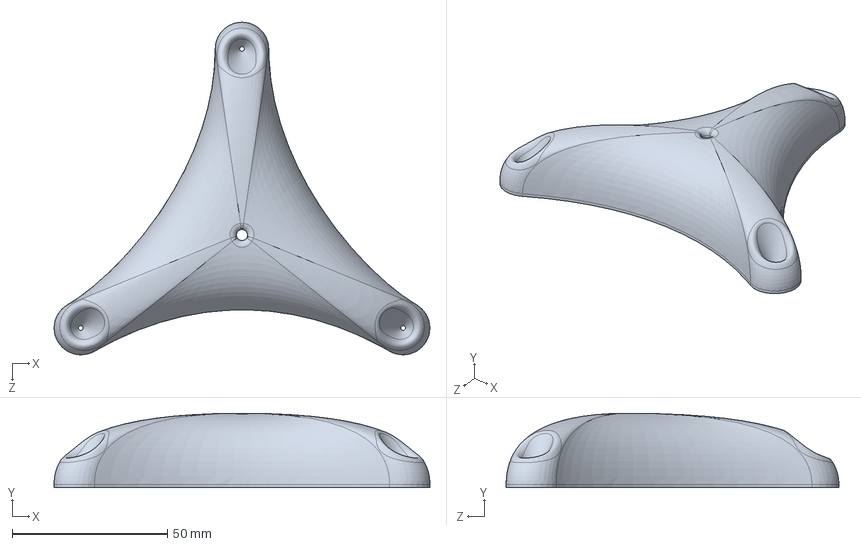
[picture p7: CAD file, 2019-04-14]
img/CAD/Designs/final_part.SLDPRT
121.3 x 24.0 x 107.3 mm

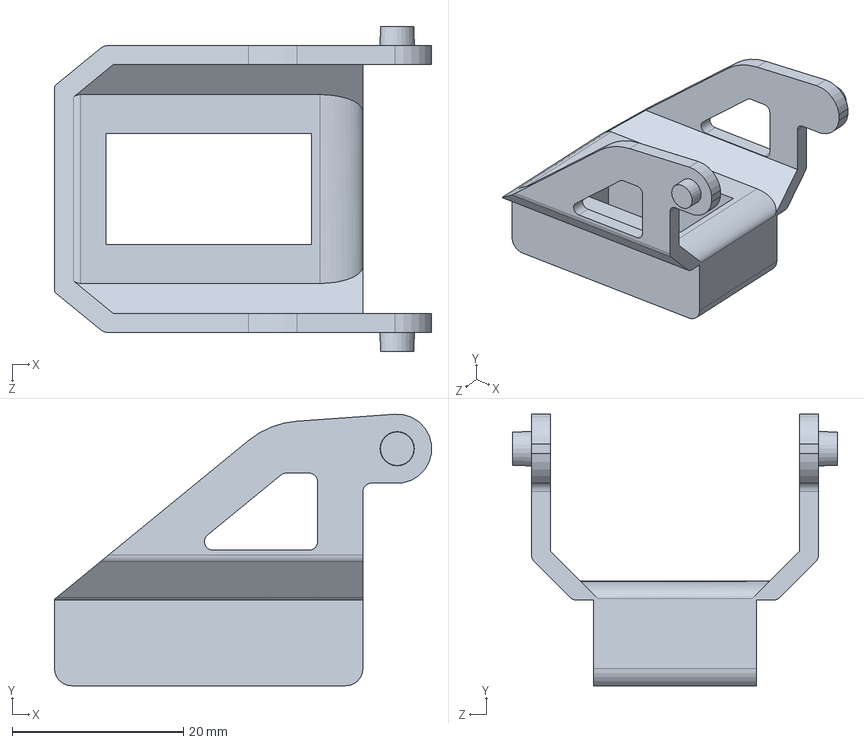
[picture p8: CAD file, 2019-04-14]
img/CAD/Designs/Gimbal mid.SLDPRT
44.0 x 31.7 x 37.9 mm

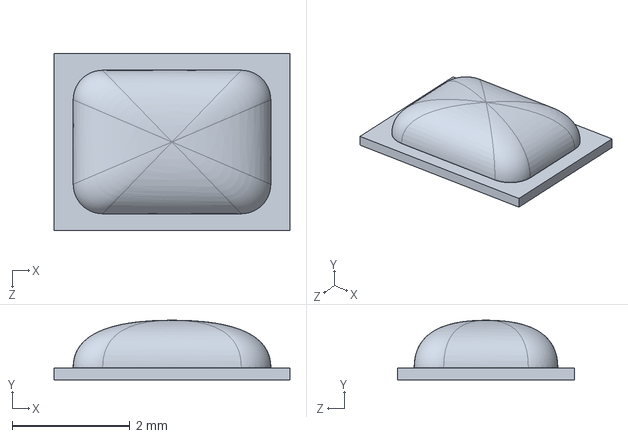
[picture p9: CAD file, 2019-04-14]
img/CAD/Designs/microphone.SLDPRT
4.00 x 1.01 x 3.00 mm

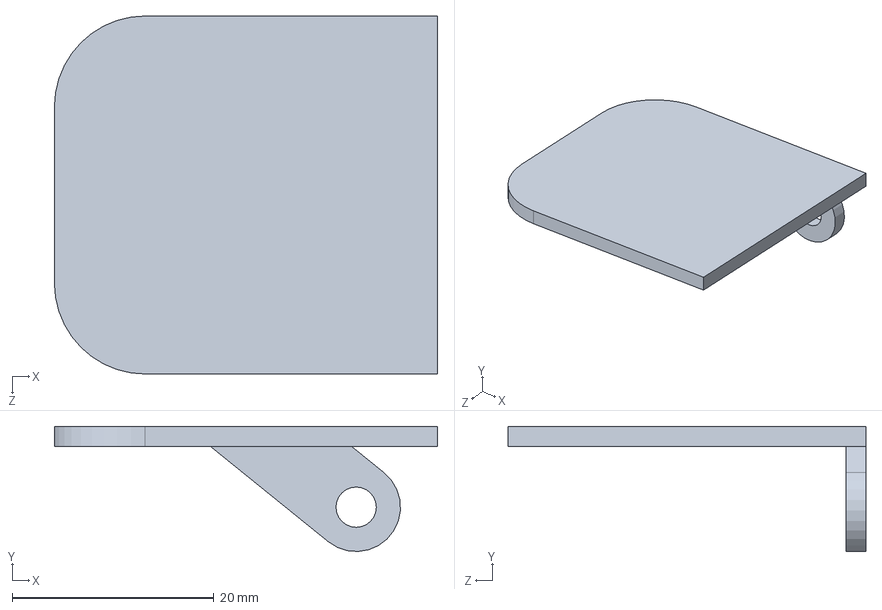
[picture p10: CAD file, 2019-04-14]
img/CAD/Designs/Gimbal top.SLDPRT
38.0 x 12.4 x 35.5 mm

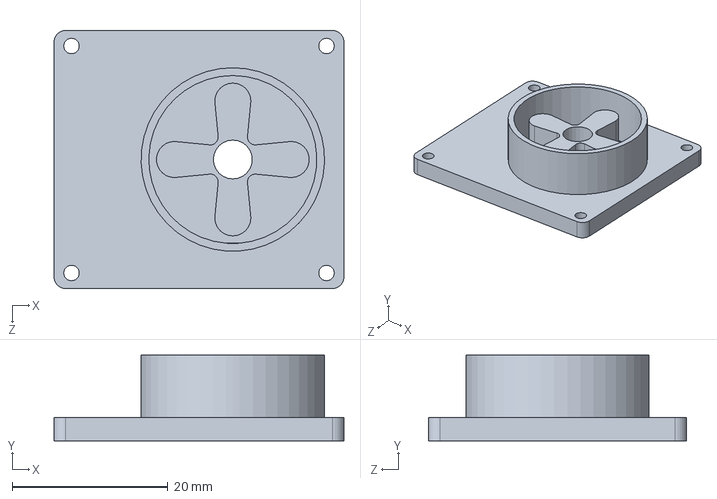
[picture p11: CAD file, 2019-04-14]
img/CAD/Designs/Gimbal Base.SLDPRT
37.3 x 11.0 x 33.2 mm

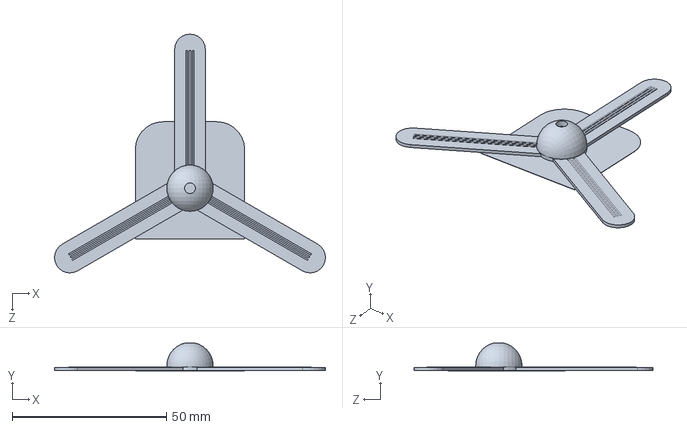
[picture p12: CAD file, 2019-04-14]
img/CAD/Designs/head.SLDPRT
87.9 x 8.99 x 77.5 mm

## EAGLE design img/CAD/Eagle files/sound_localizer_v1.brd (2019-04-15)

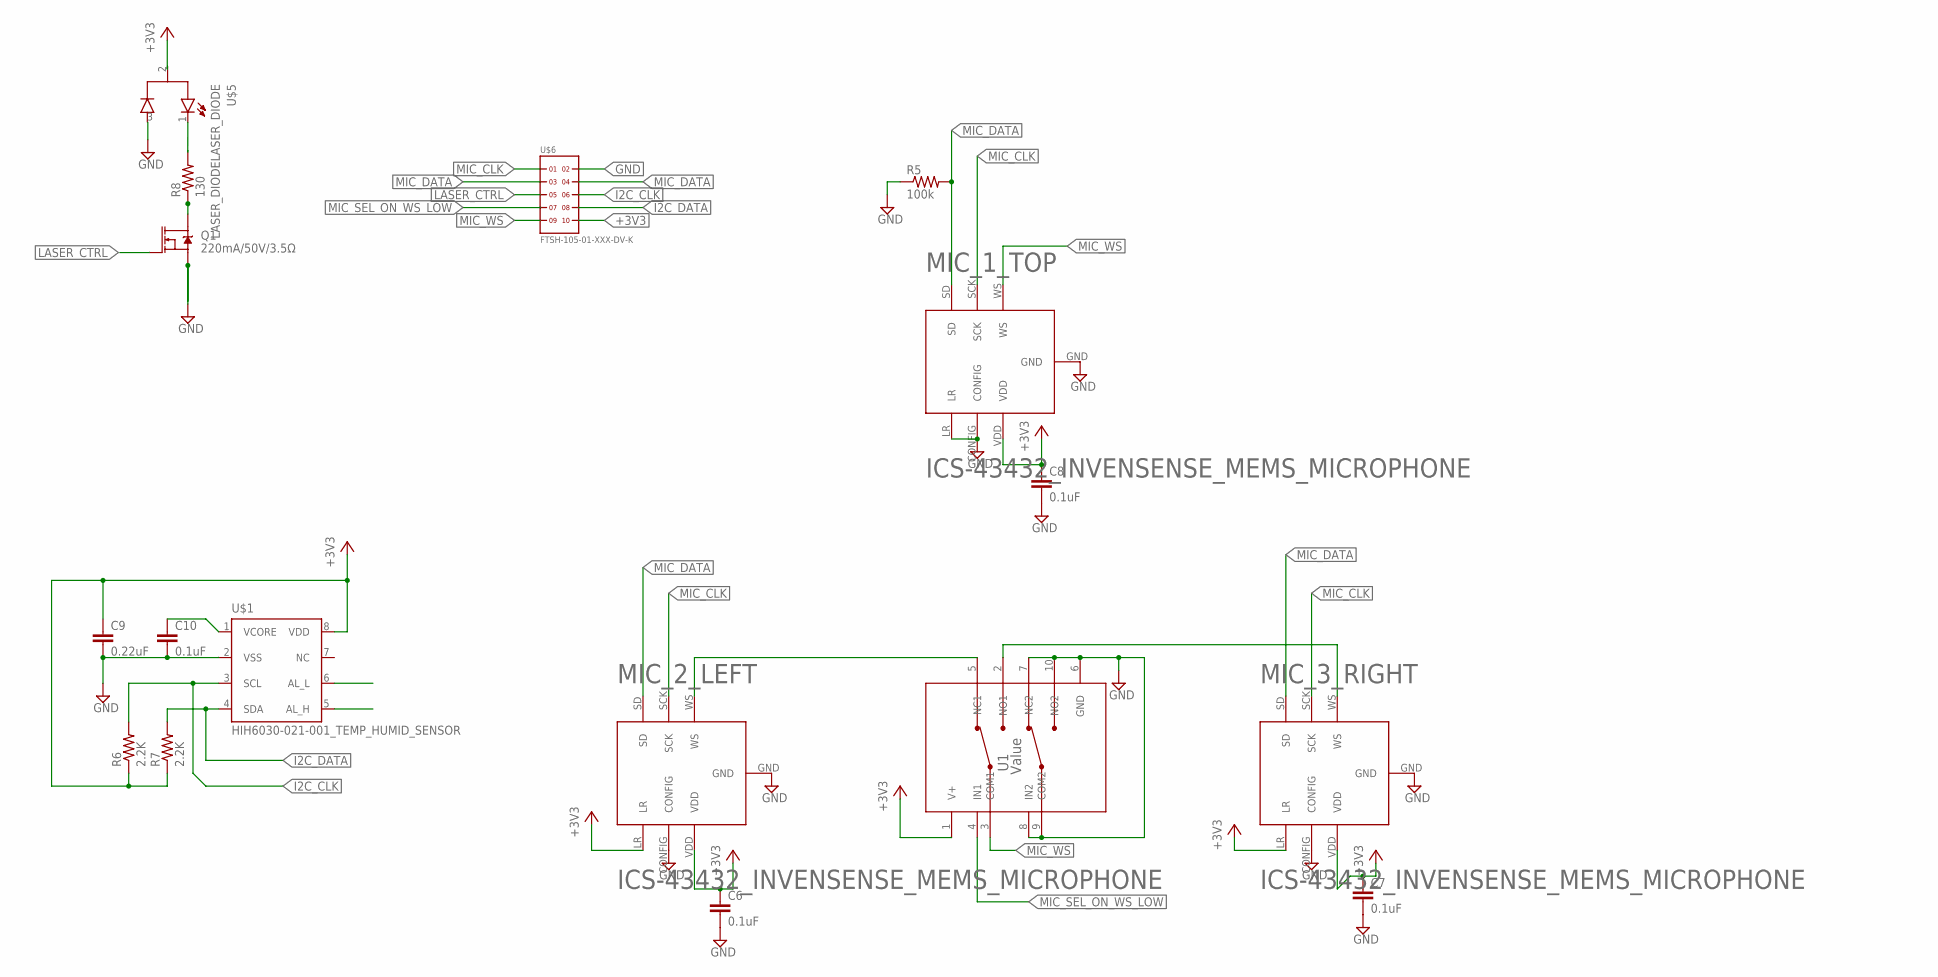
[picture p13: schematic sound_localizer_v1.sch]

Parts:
C6, C7, C8, C10: 0.1uF; C0805K
C9: 0.22uF; C0805K
MIC_1_TOP, MIC_2_LEFT, MIC_3_RIGHT: ICS-43432_INVENSENSE_MEMS_MICROPHONE; MEMS_MIC
Q1: 220mA/50V/3.5Ω; SOT23-3
R5: 100k; M0805
R6, R7: 2.2K; M0805
R8: 130; M0805
U1: Value; DGS0010A_N
U$1: HIH6030-021-001_TEMP_HUMID_SENSOR; SOIC8
U$5: LASER_DIODELASER_DIODE; TO46-LX
U$6: FTSH-105-01-XXX-DV-K

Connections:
+3V3: C6.1, C7.1, C8.1, C9.1, MIC_1_TOP.VDD, MIC_2_LEFT.LR, MIC_2_LEFT.VDD, MIC_3_RIGHT.LR, MIC_3_RIGHT.VDD, R6.1, R7.1, U1.1 (V+), U$1.8 (VDD), U$5.2, U$6.10
GND: C6.2, C7.2, C8.2, C9.2, C10.2, MIC_1_TOP.CONFIG, MIC_1_TOP.GND, MIC_1_TOP.LR, MIC_2_LEFT.CONFIG, MIC_2_LEFT.GND, MIC_3_RIGHT.CONFIG, MIC_3_RIGHT.GND, Q1.2 (S), R5.1, U1.6 (GND), U1.7 (NC2), U1.8 (IN2), U1.9 (COM2), U1.10 (NO2), U$1.2 (VSS), U$6.2
I2C_CLK: R6.2, U$1.3 (SCL), U$6.6
I2C_DATA: R7.2, U$1.4 (SDA), U$6.8
LASER_CTRL: Q1.1 (G), U$6.5
LED_CATHODE: R8.2, U$5.1
MIC_CLK: MIC_1_TOP.SCK, MIC_2_LEFT.SCK, MIC_3_RIGHT.SCK, U$6.1
MIC_DATA: MIC_1_TOP.SD, MIC_2_LEFT.SD, MIC_3_RIGHT.SD, R5.2, U$6.3, U$6.4
MIC_SEL_ON_WS_LOW: U1.4 (IN1), U$6.7
MIC_WS: MIC_1_TOP.WS, U1.3 (COM1), U$6.9
unnamed: MIC_2_LEFT.WS, U1.5 (NC1)
unnamed: MIC_3_RIGHT.WS, U1.2 (NO1)
unnamed: C10.1, U$1.1 (VCORE)
unnamed: Q1.3 (D), R8.1
NC: U$1.6 (AL_L)
P$1: U$5.3

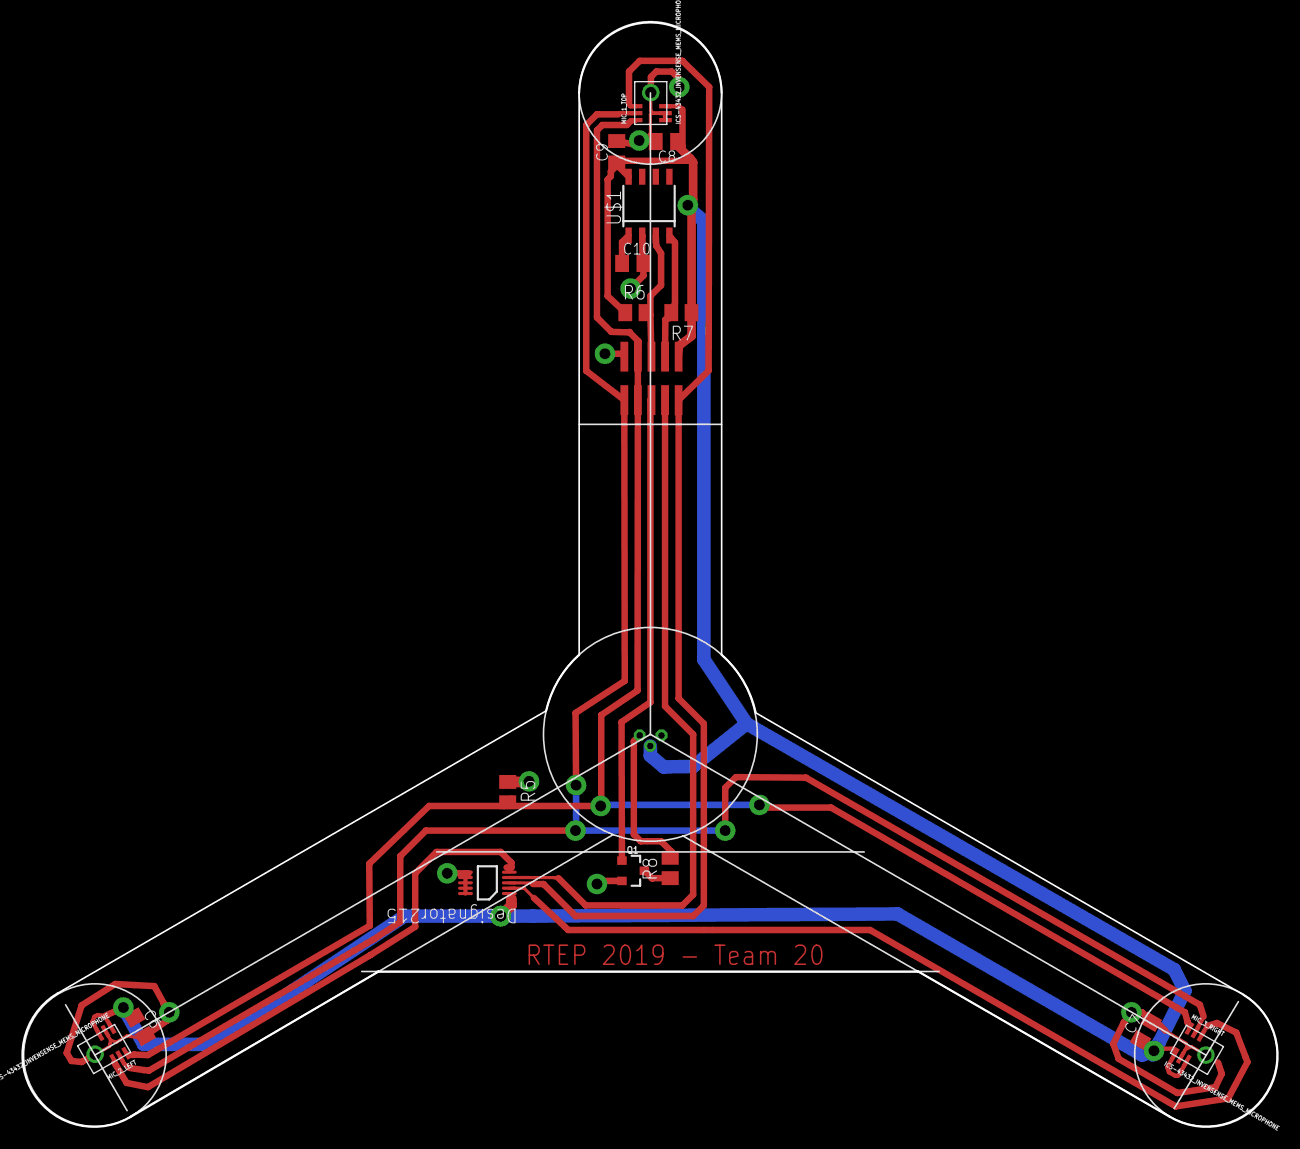
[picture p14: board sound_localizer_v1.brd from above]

Board: 2 copper layers, 117.4 x 103.3 mm, 17 parts (1 on the bottom side), 14 nets.

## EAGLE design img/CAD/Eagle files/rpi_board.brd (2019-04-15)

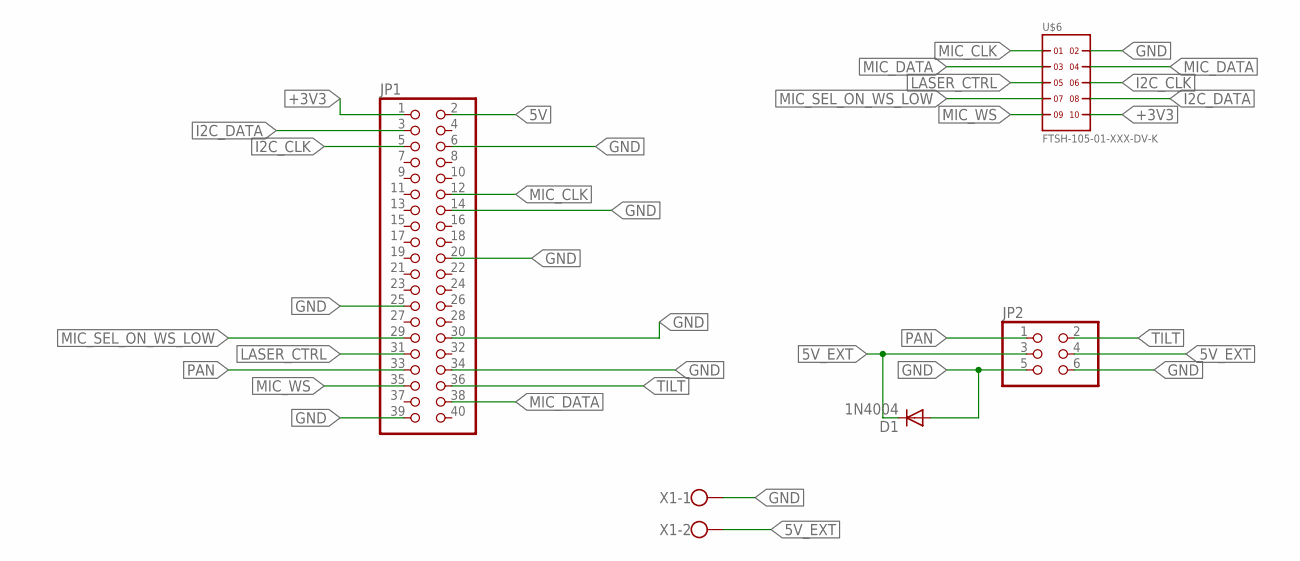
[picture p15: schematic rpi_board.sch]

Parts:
D1: 1N4004; DO41-10
JP1: PINHD-2X20; 2X20
JP2: PINHD-2X3; 2X03
U$6: FTSH-105-01-XXX-DV-K
X1: W237-102

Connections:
5V: JP1.2
5V_EXT: D1.C, JP2.3, JP2.4, X1.2
+3V3: JP1.1, U$6.10
GND: D1.A, JP1.6, JP1.14, JP1.20, JP1.25, JP1.30, JP1.34, JP1.39, JP2.5, JP2.6, U$6.2, X1.1
I2C_CLK: JP1.5, U$6.6
I2C_DATA: JP1.3, U$6.8
LASER_CTRL: JP1.31, U$6.5
MIC_CLK: JP1.12, U$6.1
MIC_DATA: JP1.38, U$6.3, U$6.4
MIC_SEL_ON_WS_LOW: JP1.29, U$6.7
MIC_WS: JP1.35, U$6.9
PAN: JP1.33, JP2.1
TILT: JP1.36, JP2.2

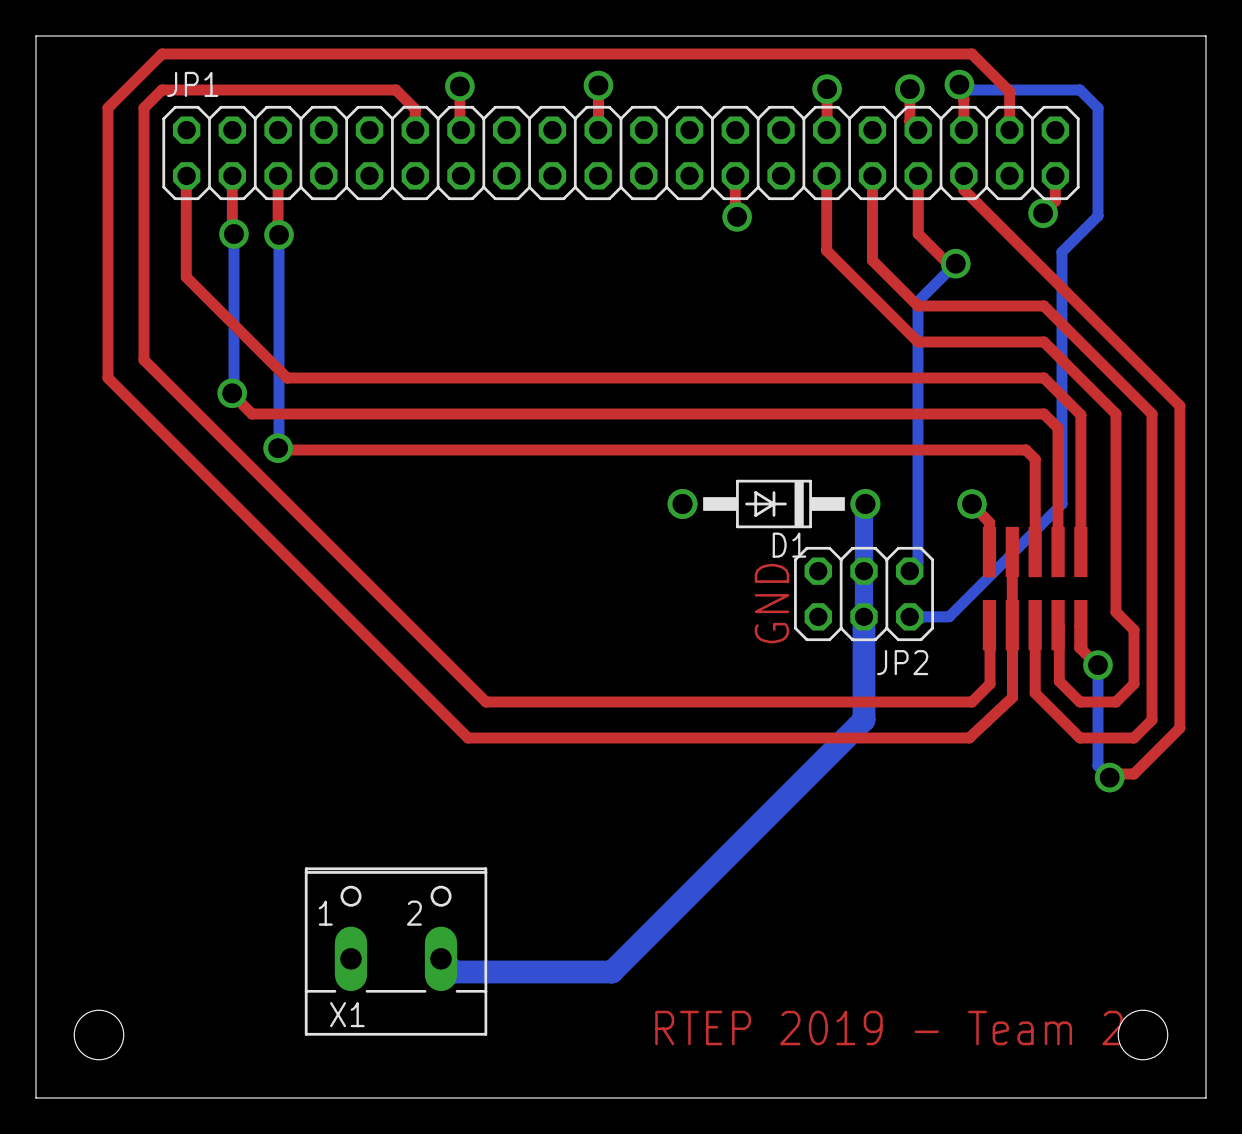
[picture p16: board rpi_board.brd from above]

Board: 2 copper layers, 65.0 x 59.0 mm, 5 parts (0 on the bottom side), 12 nets.

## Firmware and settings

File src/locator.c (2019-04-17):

/* file: locator.c */

//hardware stuff
#define DEVICE     "plughw:1" /**< Name of the ALSA PCM device. */
#define FRAMES     256 /**< Number of frames to read in. Frames contain both left- and right-channel samples and are read into the PCM buffer */
#define THRESHOLD  25000 /**< Minimum detectable sound pressure level. */
#define SAMPLERATE 44100 /**< Audio sampling frequency (Hz) */
#define TOP1       0 /**< Enumeration for top microphone buffer. (Multiplexer select = 0)*/
#define TOP2       1 /**< Enumeration for top microphone buffer. (Multiplexer select = 1)*/
#define LEFT       2 /**< Enumeration for left microphone buffer. */
#define RIGHT      3 /**< Enumeration for right microphone buffer. */

#define MUXSE      21 /**< wiringPi pin connected to multiplexer. */


#include <stdio.h>
#include <signal.h>
#include <stdlib.h>
#include <unistd.h>
#include <math.h>
#include <wiringPi.h>
#include <alsa/asoundlib.h>

#include "servo.h"
#include "utils.h"
#include "lopass.h"


FILE *out;
int debug = 0;
snd_pcm_t *handle;
snd_pcm_hw_params_t *params;
snd_pcm_uframes_t frames = FRAMES;
unsigned int sample_rate;
int sel; // mux


char *buffer;   // main ALSA PCM buffer

// buffers from microphones
signed int *top1; /**<Buffer for top mic. This buffer, along with left is read into when the multiplexer select is 0. */
signed int *top2; /**<Buffer for top mic. This buffer, along with right is read into when the multiplexer select is 1. */
signed int *left; /**<Buffer for left mic. This buffer is read into when the multiplexer select is 0. */
signed int *right; /**<Buffer for right mic. This buffer is read into when the multiplexer select is 1. */

float *top1_smooth;
float *left_smooth;
float *top2_smooth;
float *right_smooth;

//Buffer sizes
int pcm_bufsize = 0;
int mic_bufsize = 0;

// keep track of positions of both servos
int az_curr = 0;
int el_curr = 0;


// zero crossings
int zeroTop1; /**<Index of zero crossing in top1 mic buffer. */
int zeroLeft; /**<Index of zero crossing in left mic buffer. */
int zeroTop2; /**<Index of zero crossing in top2 mic buffer. */
int zeroRight;/**<Index of zero crossing in right mic buffer. */

// delays
float delTopLeft; /**<Time delay of zero crossing between top and left mics (seconds).*/
float delTopRight; /**<Time delay of zero crossing between top and right mics (seconds).*/ 
float delLeftRight; /**<Time delay of zero crossing between left and right mics (seconds).*/

// functions
//DEBUG
/**
   * A function that takes an integer buffer and renders its contents to sdout for debugging.
   * @param buf A pointer to the buffer.
   * @param size  The number of elements in the array.
   */
void printbuf(signed int *buf, int size);

/**
   * A function that takes an integer buffer and renders its contents to the specified file descriptor for debugging.
   * @param file  A pointer to a file descriptor.
   * @param buf A pointer to a signed integer.
   * @param size  The number of elements in the array.
   */
void printBufToFile(FILE *file, signed int *buf, int size);

//SERVOS AND LASER



//MICS
//int tobuf is the character code for the different buffers

/**
   * Splits data in the PCM buffer so that the correct channel is sent to the destination buffer.
   * @param tobufCode Character code for destination buffer
   * @param tobuf Pointer to destination buffer
   * @param frombuf Pointer to PCM buffer
   * @param sizefrom Size of PCM buffer
   * @see top1
   * @see top2
   * @see left
   * @see right
   */
void fillbuf(int tobufCode, int *tobuf, char *frombuf, int sizefrom); 

/**
   * Initialises the ALSA PCM interface.
   * @param device Name of the I2S device
   * @param rate Audio sampling rate (Hz)
   * @return Error code (0 on success)
   */
int setupdevice(char *device, unsigned int rate);

/**
   * Allocates memory for PCM and mic data buffers.
   * @ param frames The number of frames in the PCM buffer
   * @ param pcm_size A pointer to the integer that contains the pcm buffer size
   * @ param mic_size A pointer to the integer that contains the pcm buffer size
   * @ return Error code (0 on success)
   */ 
int setupmicbuffers(int frames, int*pcm_size, int *mic_size);

/**
   * Frees memory allocated to PCM and mic data buffers.
   */ 
void freebuffers();

/**
   * Updates top1, left, top2 and right buffers.
   */ 
void readMics(); 
/**
   * Moves servos in response to timing difference data.
   * @param delTL Time difference between sound reaching top and left mics (seconds) 
   * @param delTR Time difference between sound reaching top and right mics (seconds)
   * @param delLR Time difference between sound reaching left and right mics (seconds)
   */
void updatePosition(float delTL, float delTR, float delLR); // sets servos and LED

int main (int argc, char *argv[])
{
	if(argc == 2){
		debug = 1;
		char *filename = argv[2];
		out = fopen(filename, "w+");
	} 
	if (wiringPiSetup() == -1) exit(1);
    
    char *dev = (char *)DEVICE;
	pinMode(MUXSE, OUTPUT);
	pinMode(LASER, OUTPUT);
	pinMode(AZIMUTH, PWM_OUTPUT);
    pinMode(ELEVATION, PWM_OUTPUT);
	pwmSetup();
	setupdevice(dev, SAMPLERATE);
	setupmicbuffers(FRAMES, &pcm_bufsize, &mic_bufsize);
	laserOn();
	zeroMotors(&az_curr, &el_curr);
	delay(SERVO_DELAY); 
	stopMotors();

/*	int loops = 10000;*/
    while(1) //change to while(1) for real use
    {
    	stopMotors();
        // 1) read data from microphone
        readMics(top1, left, top2, right);

        if(debug){
	        printf("top1:\n");
		    printbuf(top1, mic_bufsize);
		    printf("left:\n");
		    printbuf(left, mic_bufsize);
		    printf("top2:\n");
		    printbuf(top2, mic_bufsize);
		    printf("right:\n");
		    printbuf(right, mic_bufsize);
        }
        // 2) if we can find 0 crossings, calculate angles, else goto 1)
        if (!findZero(top1_smooth, FRAMES, &zeroTop1, THRESHOLD)){
            continue;
        }else if(!findZero(left_smooth, FRAMES, &zeroLeft, THRESHOLD)){
            continue;
        }else if(!findZero(top2_smooth, FRAMES, &zeroTop2, THRESHOLD)){
            continue;
        }else if(!findZero(right_smooth, FRAMES, &zeroRight, THRESHOLD)){
            continue;
        }

        // 3) calculate delays
        if (!calcDelays(zeroTop1, zeroLeft, zeroTop2, zeroRight, &delTopLeft, &delTopRight, &delLeftRight, SAMPLERATE)){
            continue;
        }

        // 4) update position and turn on LED
        updatePosition(delTopLeft, delTopRight, -delLeftRight);
        //updatePosition(0, 0, delLeftRight);

        // delay for a bit to prevent jittering
        delay(SERVO_DELAY);
    }
    freebuffers();
    stopMotors();
}

void printbuf(signed int *buf, int size){
	for (int i = 0; i<size; i++){
		printf("[%d], ", buf[i]);
	}
	printf("\n\n");
}


void printBufToFile(FILE *fd, signed int *buf, int size){
	fprintf(fd, "[");
	for (int i = 0; i<size; i++){
		fprintf(fd, "%d, ", buf[i]);
	}
	fprintf(fd, "]\n");
}

int setupdevice(char *device, unsigned int rate){
	int err;
    sample_rate = rate;


    printf("req period size: %d\n", frames);
	printf("req sample rate: %d\n", sample_rate);
    /* Open PCM device for recording (capture). */
    err = snd_pcm_open(&handle, device, SND_PCM_STREAM_CAPTURE, 0);
    if (err)
    {
        fprintf(stderr, "Unable to open PCM device: %s\n", snd_strerror(err));
        return err;
    }

    /* Allocate a hardware parameters object. */
    snd_pcm_hw_params_alloca(&params);

    /* Fill it in with default values. */
    snd_pcm_hw_params_any(handle, params);

    /* ### Set the desired hardware parameters. ### */

    /* Interleaved mode */
    err = snd_pcm_hw_params_set_access(handle, params, SND_PCM_ACCESS_RW_INTERLEAVED);
    if (err<0)
    {
        fprintf(stderr, "Error setting interleaved mode: %s\n", snd_strerror(err));
        snd_pcm_close(handle);
        return err;
    }
    /* Signed 16-bit big-endian format */
    err = snd_pcm_hw_params_set_format(handle, params, SND_PCM_FORMAT_S16_BE);
    if (err<0)
    {
        fprintf(stderr, "Error setting format: %s\n", snd_strerror(err));
        snd_pcm_close(handle);
        return err;
    }
    /* Two channels (stereo) */
    err = snd_pcm_hw_params_set_channels(handle, params, 2);
    if (err<0)
    {
        fprintf(stderr, "Error setting channels: %s\n", snd_strerror(err));
        snd_pcm_close(handle);
        return err;
    }
    /* 44100 bits/second sampling rate (CD quality) */
    err = snd_pcm_hw_params_set_rate_near(handle, params, &sample_rate, NULL);
    if (err<0)
    {
        fprintf(stderr, "Error setting sampling rate (%d): %s\n", sample_rate, snd_strerror(err));
        snd_pcm_close(handle);
        return err;
    }
    /* Set period size*/
    err = snd_pcm_hw_params_set_period_size_near(handle, params, &frames, NULL);
    if (err<0)
    {
        fprintf(stderr, "Error setting period size: %s\n", snd_strerror(err));
        snd_pcm_close(handle);
        return err;
    }

    unsigned int periodtime;
    snd_pcm_hw_params_get_period_time(params, &periodtime, NULL);
    printf("period time: %dus\n", periodtime);

    printf("actual period size: %d\n", frames);
	printf("actual sample rate: %d\n", sample_rate);

    /* Write the parameters to the driver */
    err = snd_pcm_hw_params(handle, params);
    if (err<0)
    {
        fprintf(stderr, "Unable to set HW parameters: %s\n", snd_strerror(err));
        snd_pcm_close(handle);
        return err;
    }

}

int setupmicbuffers(int frames, int *pcm_size, int *mic_size){
	int err;

    *pcm_size = frames * 2 * 2; /* 2 bytes/sample, 2 channels */
    *mic_size = frames; // one int per frame received
    int size_mic_bytes = frames *  sizeof(signed int);
    int size_smooth_bytes = frames * sizeof(float);

    printf("main_buffer_size: %d bytes (%d samples)\n", pcm_bufsize, pcm_bufsize/2);
    printf("mic_buffers_size: %d bytes (%d ints)\n", size_mic_bytes, frames);
    printf("smooth_buffer_size: %d bytes (%d floats)\n", size_smooth_bytes, frames);
    buffer = (char *) malloc(*pcm_size);
    if (!buffer)
    {
        fprintf(stdout, "Buffer error.\n");
        snd_pcm_close(handle);
        return -1;
    }
    

    top1 = (signed int *) malloc(size_mic_bytes);
    if (!top1)
    {
        fprintf(stdout, "Buffer error.\n");
        snd_pcm_close(handle);
        return -1;
    }

    top2 = (signed int *) malloc(size_mic_bytes);
    if (!top2)
    {
        fprintf(stdout, "Buffer error.\n");
        snd_pcm_close(handle);
        return -1;
    }

    left = (signed int *) malloc(size_mic_bytes);
    if (!left)
    {
        fprintf(stdout, "Buffer error.\n");
        snd_pcm_close(handle);
        return -1;
    }

    right = (signed int *) malloc(size_mic_bytes);
    if (!right)
    {
        fprintf(stdout, "Buffer error.\n");
        snd_pcm_close(handle);
        return -1;
    }
    
    top1_smooth = (float *) malloc(size_smooth_bytes);
    if (!top1_smooth)
    {
        fprintf(stdout, "Buffer error.\n");
        snd_pcm_close(handle);
        return -1;
    }
    
    top2_smooth = (float *) malloc(size_smooth_bytes);
    if (!top2_smooth)
    {
        fprintf(stdout, "Buffer error.\n");
        snd_pcm_close(handle);
        return -1;
    }
    
    left_smooth = (float *) malloc(size_smooth_bytes);
    if (!left_smooth)
    {
        fprintf(stdout, "Buffer error.\n");
        snd_pcm_close(handle);
        return -1;
    }
    
    right_smooth = (float *) malloc(size_smooth_bytes);
    if (!right_smooth)
    {
        fprintf(stdout, "Buffer error.\n");
        snd_pcm_close(handle);
        return -1;
    }


    return 0;
}

void freebuffers(){
	free(buffer);
    free(top1);
    free(top2);
	free(left);
	free(right);
	free(top1_smooth);
    free(top2_smooth);
	free(left_smooth);
	free(right_smooth);
}

//(char code for sub buffer to fill, main buffer, size of main buffer)
void fillbuf(int tobufCode, int *tobuf, char *frombuf, int sizefrom){
	switch(tobufCode){
		char lsb;
		char msb;
		int  value;
		case TOP1:
			for(int i = 0; i < sizefrom; i+=4){
				lsb   = frombuf[i];
				msb   = frombuf[i+1];
				value = convertValue(msb, lsb);
				tobuf[i/4] = value;
			}
			break;

		case TOP2:
			for(int i = 0; i < sizefrom; i+=4){
				lsb   = frombuf[i];
				msb   = frombuf[i+1];
				value = convertValue(msb, lsb);
				tobuf[i/4] = value;
			}
			break;

		case LEFT:
			for(int i = 2; i < sizefrom; i+=4){
				lsb = frombuf[i];
				msb = frombuf[i+1];
				value = convertValue(msb, lsb);
				tobuf[((i+2)/4) - 1] = value;
			}
			break;

		case RIGHT:
			for(int i = 2; i < sizefrom; i+=4){
				lsb = frombuf[i];
				msb = frombuf[i+1];
				value = convertValue(msb, lsb);
				tobuf[((i+2)/4) - 1] = value;
			}
			break;

		default:
			printf("Unknown buffer: %c\n", tobuf);
	}
}


//fills top1, left, top2 and right buffers
void readMics(int *top1, int *left, int *top2, int *right)
{
	int err;
    sel = 1;
	digitalWrite(MUXSE, sel);
	err = snd_pcm_readi(handle, buffer, frames);
	if (debug) printf("mux: %d, read %d frames to buffer\n", sel, err);
    fillbuf(TOP1, top1, buffer, pcm_bufsize);
    fillbuf(LEFT, left, buffer, pcm_bufsize);
    lowpass(top1, top1_smooth, frames);
    lowpass(left, left_smooth, frames);

	sel = 0;
	digitalWrite(MUXSE, sel);
	err = snd_pcm_readi(handle, buffer, frames);
	if (debug) printf("mux: %d, read %d frames to buffer\n", sel, err);
	fillbuf(TOP2, top2, buffer, pcm_bufsize);
	fillbuf(RIGHT, right, buffer, pcm_bufsize);
	lowpass(top2, top2_smooth, frames);
    lowpass(right, right_smooth, frames);

    if (err == -EPIPE) fprintf(stderr, "Overrun occurred: %d\n", err);
    if (err < 0) err = snd_pcm_recover(handle, err, 0);
    // Still an error, need to exit.
    if (err < 0)
    {
        fprintf(stderr, "Error occured while recording: %s\n", snd_strerror(err));
        snd_pcm_close(handle);
        freebuffers();
    }
}


// args -- (delay between top mic and left, delay between top mic and right, delay between left mic and right) in us
void updatePosition(float delTL, float delTR, float delLR){
    int azimuth_angle   = round(getDevFromNormal(delLR));
    int elevation_angle;
    
    if (delTL > delTR){
    	elevation_angle = round(getDevFromNormal(delTL));
    }else{
    	elevation_angle = round(getDevFromNormal(delTR));
    }
    
    turnMotorBy(azimuth_angle, AZIMUTH, &az_curr);
    turnMotorBy(elevation_angle, ELEVATION, &el_curr);
    laserOn();
    printf("azimuth deviation: %d degrees\n", azimuth_angle);
    printf("elevation deviation: %d degrees\n", elevation_angle);
}

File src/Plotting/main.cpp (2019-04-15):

#include "mainwindow.h"
#include <QApplication>

#include <string>
#include <sstream>
#include <iostream>
#include <vector>
#include <fstream>

#include <QDebug>
#include <QString>
#include <QFile>
#include <QStringList>
#include <QDir>
#include <QVarLengthArray>

int main(int argc, char *argv[])
{



    QApplication a(argc, argv);
    MainWindow w;
    w.show();

    return a.exec();
}

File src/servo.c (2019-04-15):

#ifdef TEST
#define TURNMOTORTO mock_turnMotorTo
#else
#define TURNMOTORTO turnMotorTo
#endif

#include "servo.h"
#include <wiringPi.h>
#include <stdlib.h>
#include <stdio.h>

//Mock function for testing
void mock_turnMotorTo(int angle, int motor){
	return;
}

//Function definitions


int getPwmClk(int pwmRange){
    return BASE_CLK/(pwmRange * PWM_FREQ);
}


int getPwmValue(int angle){  // from -90 to +90
    if (angle > 90){
    	printf("err: Max angle is 90\n");
    	exit(-1);
    }

    if (angle < -90){
    	printf("err: Min angle is -90\n");
    	exit(-1);
    }

    return 160 - angle;

}

void turnMotorTo(int angle, int motor){
    int toWrite = getPwmValue(angle);
    pwmWrite(motor, toWrite);
    printf("angle: %d - pwmVal: %d\n", angle,  toWrite);
}

void stopMotor(int pin){
    pwmWrite(pin, 0);
}

void stopMotors(){
	stopMotor(AZIMUTH);
	stopMotor(ELEVATION);
}

void turnMotorBy(int angle, int motor, int *curr){
	int new_angle;
	switch(motor){
    	case AZIMUTH:
    		new_angle = *curr + angle;
    		if(new_angle >= AZ_MIN && new_angle <= AZ_MAX){
    			*curr = new_angle;
    			TURNMOTORTO(*curr, AZIMUTH);
    		}else if(new_angle > AZ_MAX){
    			*curr = AZ_MAX;
    			TURNMOTORTO(*curr, AZIMUTH);
    		}else if(new_angle < AZ_MIN){
    			*curr = AZ_MIN;
    			TURNMOTORTO(*curr, AZIMUTH);
    		}
    		break;

    	case ELEVATION:
    		new_angle = *curr + angle;
    		if(new_angle >= EL_MIN && new_angle <= EL_MAX){
    			*curr = new_angle;
    			TURNMOTORTO(*curr, ELEVATION);
    		}else if(new_angle > EL_MAX){
    			*curr = EL_MAX;
    			TURNMOTORTO(*curr, ELEVATION);
    		}else if(new_angle < EL_MIN){
    			*curr = EL_MIN;
    			TURNMOTORTO(*curr, ELEVATION);
    		}
    		break;
    	default:
    		printf("Motor not found: %d\n", motor);
    }
}

void zeroAzimuth(int *curr){
	turnMotorTo(0, AZIMUTH);
	*curr = 0;
}

void zeroElevation(int *curr){
	turnMotorTo(0, ELEVATION);
	*curr = 0;
}

void zeroMotors(int *az_curr, int *el_curr){
	zeroAzimuth(az_curr);
	zeroElevation(el_curr);
}

void pwmSetup(){
    pwmSetMode(PWM_MODE_MS);
    pwmSetRange(PWMRNG);
    int clk = getPwmClk(PWMRNG);
    pwmSetClock(clk);
    printf("pwm_range: %d\npwm_clk: %d\n", PWMRNG, clk);
}

void laserOn(){
	digitalWrite(LASER, 1);
}

void laserOff(){
	digitalWrite(LASER, 0);
}

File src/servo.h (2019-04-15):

#ifndef SERVO_H
#define SERVO_H

#define LASER      22 /**< wiringPi pin connected to LED. */
#define ELEVATION  23 /**< wiringPi pin connected to top servo. */
#define AZIMUTH    26 /**< wiringPi pin connected to bottom servo. */
#define BASE_CLK   19200000 /**< Raspberry Pi base clock frequency (Hz). */
#define PWM_FREQ   50  /**< Desired PWM frequency (Hz). */
#define PWMRNG     2000 /**< Range of PWM period. */
#define AZ_MAX     90  /**<Maximum azimuthal angle (degrees). Used in limiting range of motion to prevent damage.*/
#define AZ_MIN    -90  /**<Minimum azimuthal angle (degrees). Used in limiting range of motion to prevent damage.*/
#define EL_MAX     70 /**<Maximum elevation angle (degrees). Used in limiting range of motion to prevent damage.*/
#define EL_MIN    -35 /**<Minimum elevation angle (degrees). Used in limiting range of motion to prevent damage.*/
#define DELAY      250  /**<Servo delay (milliseconds). Used in preventing jitter.*/


//Function signatures
/**
   * Sets up PWM control for the servo motors.
   */
void pwmSetup();

/**
   * Turns on the front LED.
   */
void laserOn();

/**
   * Turns off the front LED.
   */
void laserOff();

/**
   * Stops movement of both servos.
   */
void stopMotors();

/**
   * Brings both servos to their 0 position, i.e. facing straight ahead.
   * @param az_curr current position of azimuthal motor (degrees) 
   * @param el_curr current position of elevation motor (degrees)
   */
void zeroMotors(int *az_curr, int *el_curr);

/**
   * Turns a given motor by the specified angle in degrees. Prevents movements of the servos at their angular limits so as to avoid damage
   * @param angle The angle by which the motor should turn. 
   * @param motor An integer that distiguishes between the azimuthal or elevation servo.
   * @param curr The current angular position of the servo
   * @see AZIMUTH
   * @see ELEVATION
   */
void turnMotorBy(int angle, int motor, int *curr); // 



void zeroAzimuth(int *curr);
void zeroElevation(int *curr);
int  getPwmClk(int pwmRange);
int  getPwmValue(int angle);
void turnMotorTo(int angle, int motor);
void stopMotor(int motor);

#endif

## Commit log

2019-01-29 added CAD images
2019-02-07 Implements test code that verifies SPI communication between MCP3208 ADC and RPi
2019-02-14 established communication between i2s temp sensor and Rpi
2019-02-26 abstracted mux threads away into separate functions
2019-04-09 added sample code
2019-04-10 can set device and duration from cmd
2019-04-10 plot 2 channel audio from a csv
    [leftblocked.csv, unblocked.csv]
2019-04-11 filter main stereo buffer into 3 mono buffer
2019-04-12 functions for servos
2019-04-12 minimal unit testing framework
2019-04-12 added csv files
    [centre64.csv, left64.csv, right64.csv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]
2019-04-14 added part of the servo code
2019-04-14 cad added
    [Gimbal Base.SLDPRT, Gimbal assembly.SLDASM, Gimbal mid.SLDPRT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]
2019-04-14 fixed some isues with servo control
2019-04-14 add laser control
2019-04-14 fixed peak detection bug
    [locator.c]
2019-04-14 bugs in calcDelay() function
    [locator.c]
2019-04-15 move servo specifc code
2019-04-15 remove temp sensor code
2019-04-15 csv files
    [centre64.csv, left64.csv, right64.csv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]
2019-04-15 eagle schematic files added
    [rpi_board.sch, sound_localizer_v1.sch]
2019-04-15 eagle board files added
    [rpi_board.brd, sound_localizer_v1.brd]
2019-04-15 add unit test for servo motors

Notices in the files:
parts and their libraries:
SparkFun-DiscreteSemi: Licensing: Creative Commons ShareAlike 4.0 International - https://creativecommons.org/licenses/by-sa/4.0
